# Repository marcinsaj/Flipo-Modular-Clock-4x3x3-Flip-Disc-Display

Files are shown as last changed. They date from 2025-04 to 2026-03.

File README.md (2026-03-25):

# Modular Flip-Disc Clock

>[!TIP]
> If you have issues powering the clock, see the list of [compatible power adapters](https://github.com/marcinsaj/Flipo-Modular-Clock-4x3x3-Flip-Disc-Display/blob/main/datasheet/verified-compatible-power-adapters.md).

## Specification
- the clock consists of two modules: controller module & flip-disc display module
- two buttons for setting the time
- one button for turning on the clock
- accurate real-time clock (RTC) on board RX8025T
- the RTC clock memory is backed up by a supercapacitor, so the clock does not require an additional battery in the event of a power failure or turn off
- clock dimensions: 53 x 137 x 142mm (2.1" x 5.4" x 5.6")
- power supply from USB-C PD 12V
- ISP programming connector - only for intermediate users

## 3D Printed Enclosure
You can print your own enclosure or modify the design:
- [Download STL files on Printables](https://www.printables.com/model/1650064-modular-flip-disc-clock-enclosure)
- [Download the Fusion 360 source file](https://github.com/marcinsaj/Flipo-Modular-Clock-4x3x3-Flip-Disc-Display/raw/main/datasheet/enclosure-modular-flip-disc-clock.f3d)

## Datasheet
  - [CLOCK USER MANUAL](https://github.com/marcinsaj/Flipo-Modular-Clock-4x3x3-Flip-Disc-Display/raw/main/datasheet/Manual-Modular-Flip-Disc-Clock.pdf)
  - [HOW TO READ THE DISPLAY](https://github.com/marcinsaj/Flipo-Modular-Clock-4x3x3-Flip-Disc-Display/raw/main/datasheet/Modular-Flip-Disc-Clock-Symbols.pdf)
  - [FIRMWARE](https://github.com/marcinsaj/Flipo-Modular-Clock-4x3x3-Flip-Disc-Display/blob/main/examples/Firmware-Modular-Flip-Disc-Clock.ino)
  - [4x3x3 flip-disc display module v1 - outdated](https://github.com/marcinsaj/Flipo-Modular-Clock-4x3x3-Flip-Disc-Display/raw/main/datasheet/Modular-Flip-disc-Clock-4x3x3-Display-Module-Schematic-v1.pdf)
  - [4x3x3 flip-disc display module v2 - current version](https://github.com/marcinsaj/Flipo-Modular-Clock-4x3x3-Flip-Disc-Display/raw/main/datasheet/Modular-Flip-disc-Clock-4x3x3-Display-Module-Schematic-v2.pdf)
  - [4x3x3 flip-disc controller module v1 - outdated](https://github.com/marcinsaj/Flipo-Modular-Clock-4x3x3-Flip-Disc-Display/raw/main/datasheet/Modular-Flip-disc-Clock-4x3x3-Controller-Module-Schematic-v1.pdf)
  - [4x3x3 flip-disc controller module v5 - current version](https://github.com/marcinsaj/Flipo-Modular-Clock-4x3x3-Flip-Disc-Display/raw/main/datasheet/Modular-Flip-disc-Clock-4x3x3-Controller-Module-Schematic-v5.pdf)

## Programming and Firmware
If you want to modify the [firmware](https://github.com/marcinsaj/Flipo-Modular-Clock-4x3x3-Flip-Disc-Display/blob/main/examples/Firmware-Modular-Flip-Disc-Clock.ino), you can program the clock via the ISP connector.

### MiniCore Configuration
Before burning the bootloader, install MiniCore using the following Boards Manager URL:
https://mcudude.github.io/MiniCore/package_MCUdude_MiniCore_index.json

### In Arduino IDE → Tools, configure the settings as follows:
- Board: ATmega328P / ATmega328PA
- Clock: External 12 MHz ⚠
- Bootloader: Yes (UART0)
- BOD: 2.7V
- EEPROM: Retained
- Compiler LTO: Enabled
- Baud Rate: Default
- Variant: 328P / 328PA

⚠ Make sure the clock is set to External 12 MHz. ⚠

## Programming Procedure:
 1. Select the correct Programmer: AVR ISP MKII (recommended).
 2. Click Burn Bootloader to set the fuse bits and configure the microcontroller.
 3. After completion, select Upload Using Programmer to flash the firmware.

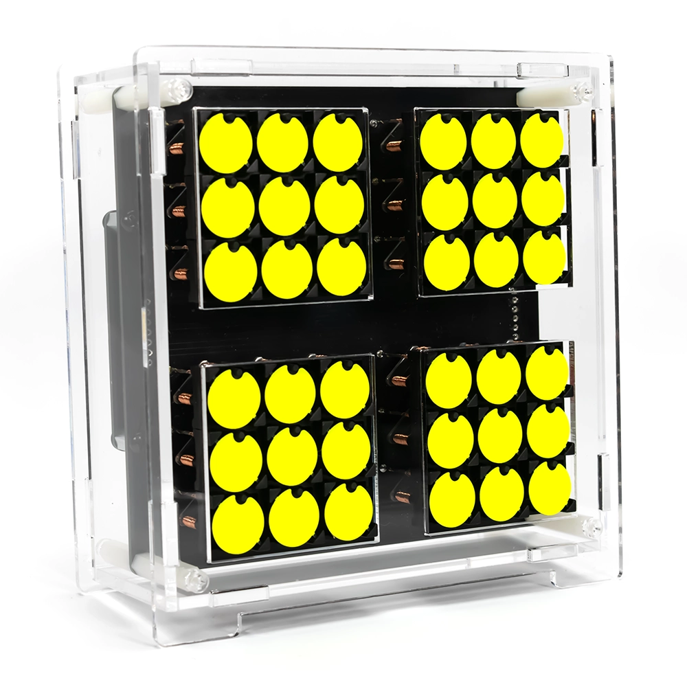
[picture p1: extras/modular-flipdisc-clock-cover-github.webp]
Modular Flip-disc Clock

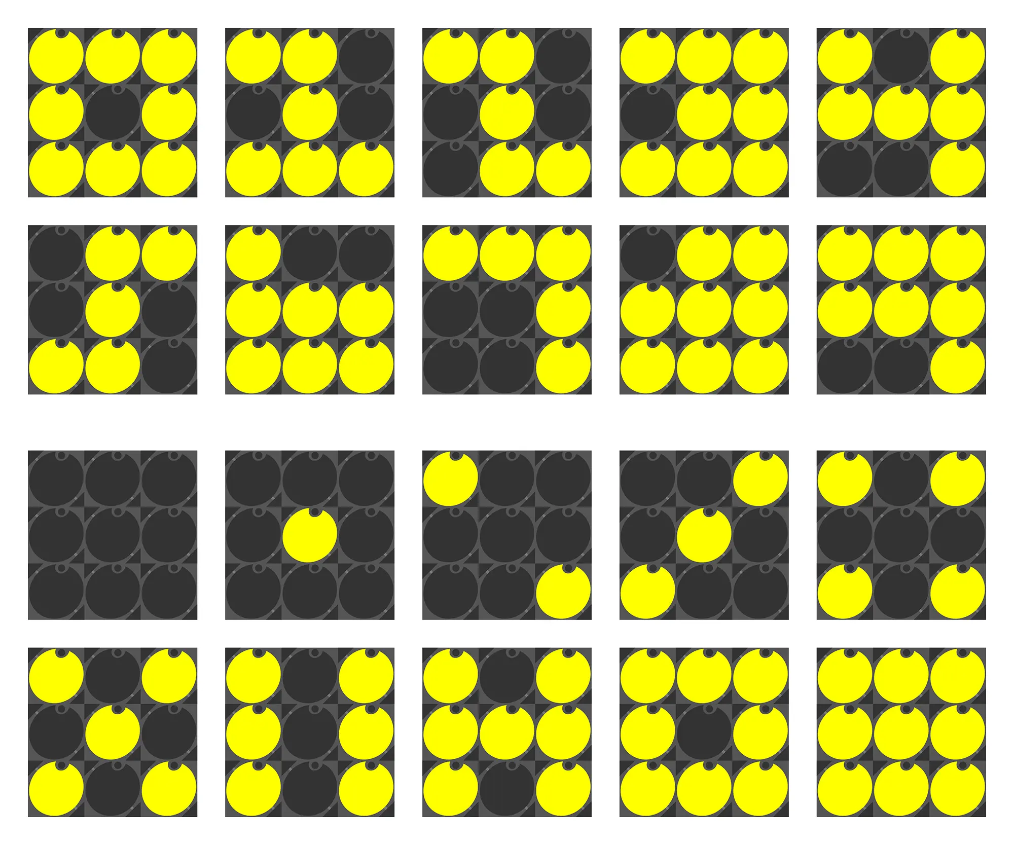
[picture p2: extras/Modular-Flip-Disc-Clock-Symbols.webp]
Modular Flip-disc Clock - Digits

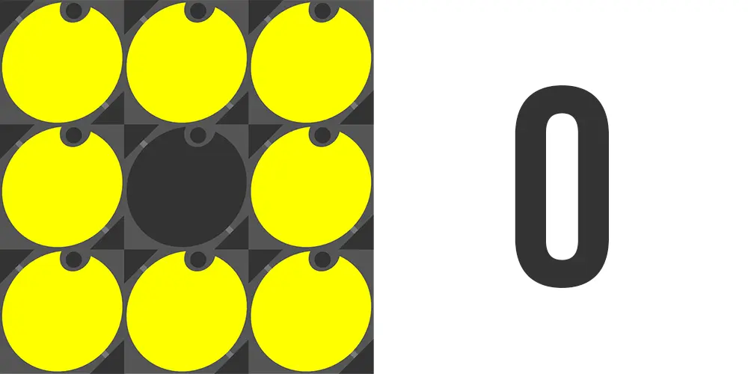
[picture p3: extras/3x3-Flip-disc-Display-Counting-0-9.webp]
Modular Flip-disc Clock - 3x3 Module

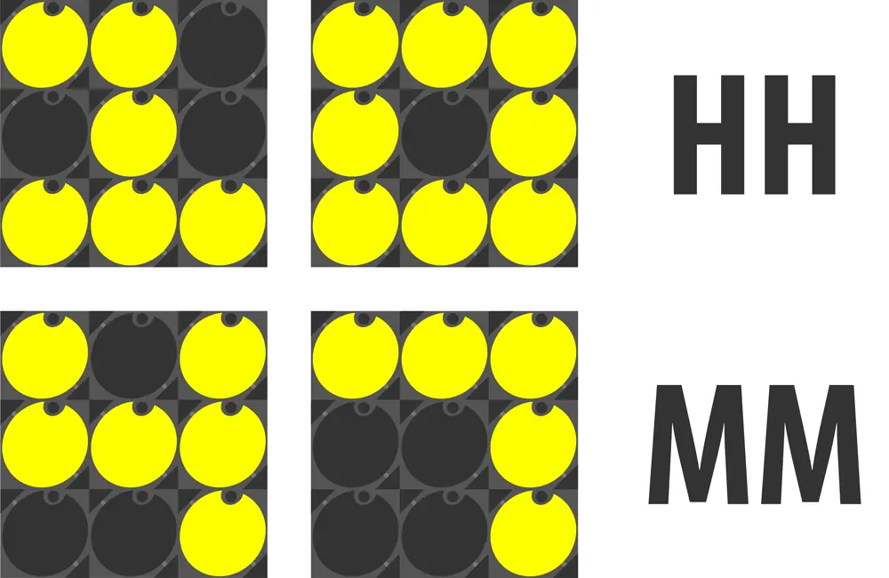
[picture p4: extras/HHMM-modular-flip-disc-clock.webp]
Modular Flip-disc Clock - HH:MM


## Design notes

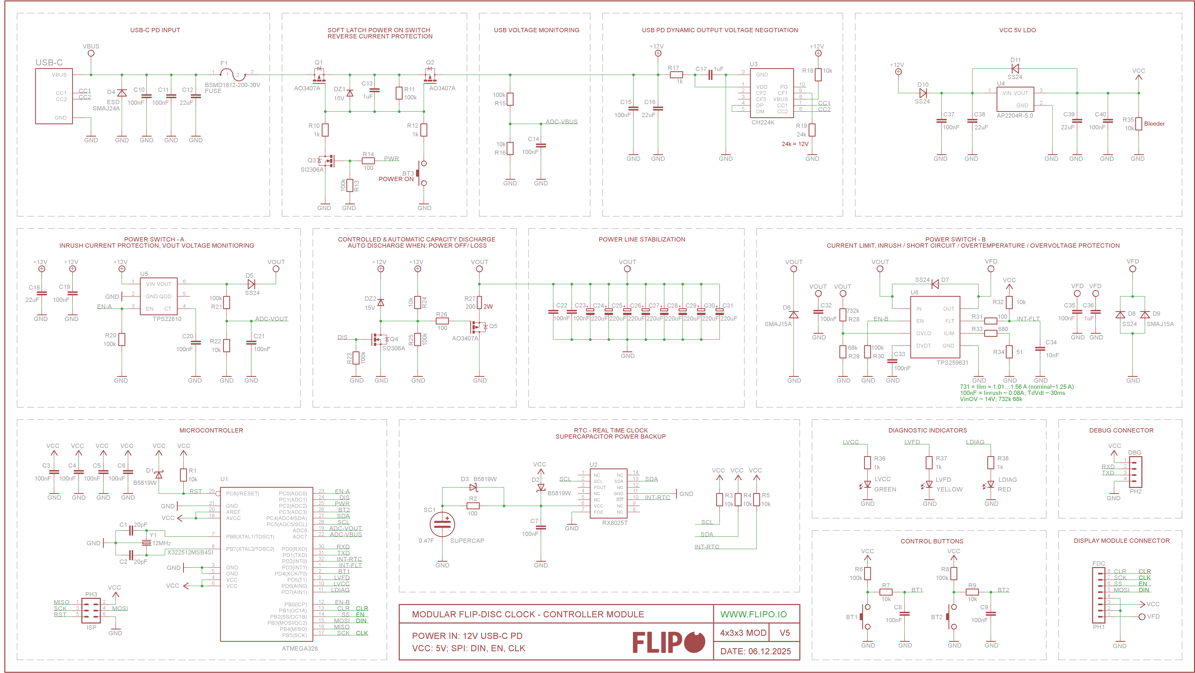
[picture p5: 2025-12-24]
datasheet/Modular-Flip-disc-Clock-4x3x3-Controller-Module-Schematic-v5.png

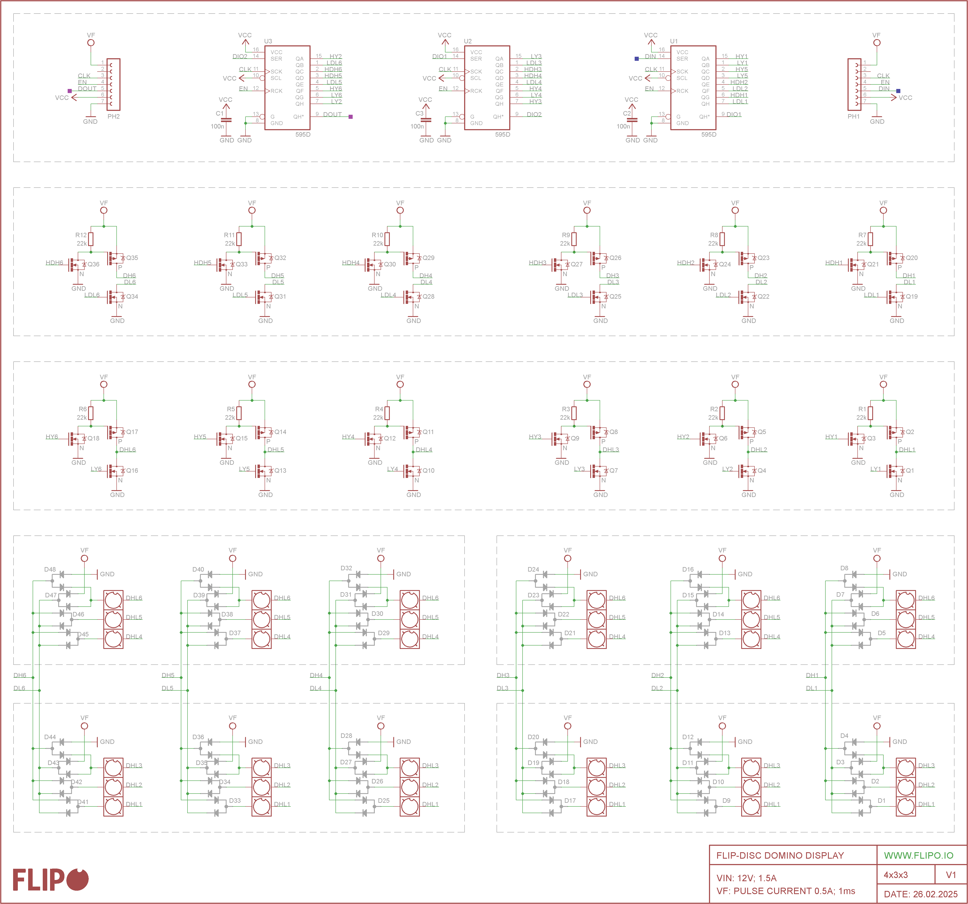
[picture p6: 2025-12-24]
datasheet/Modular-Flip-disc-Clock-4x3x3-Display-Module-Schematic-v1.png

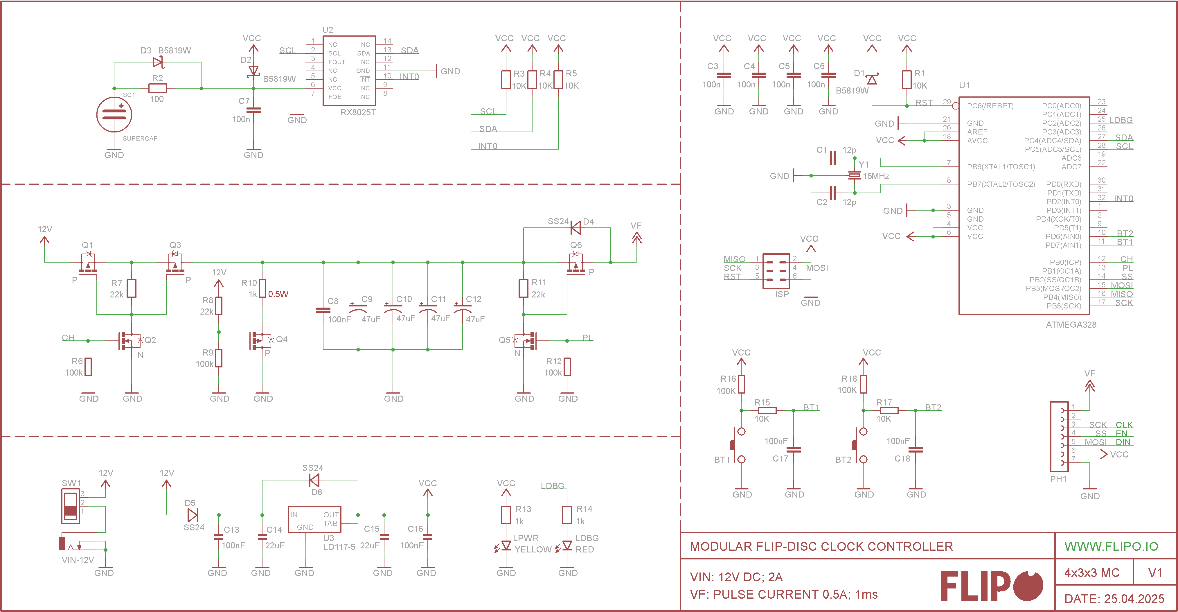
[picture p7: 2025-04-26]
datasheet/Modular-Flip-disc-Clock-4x3x3-Controller-Module-Schematic-v1.png

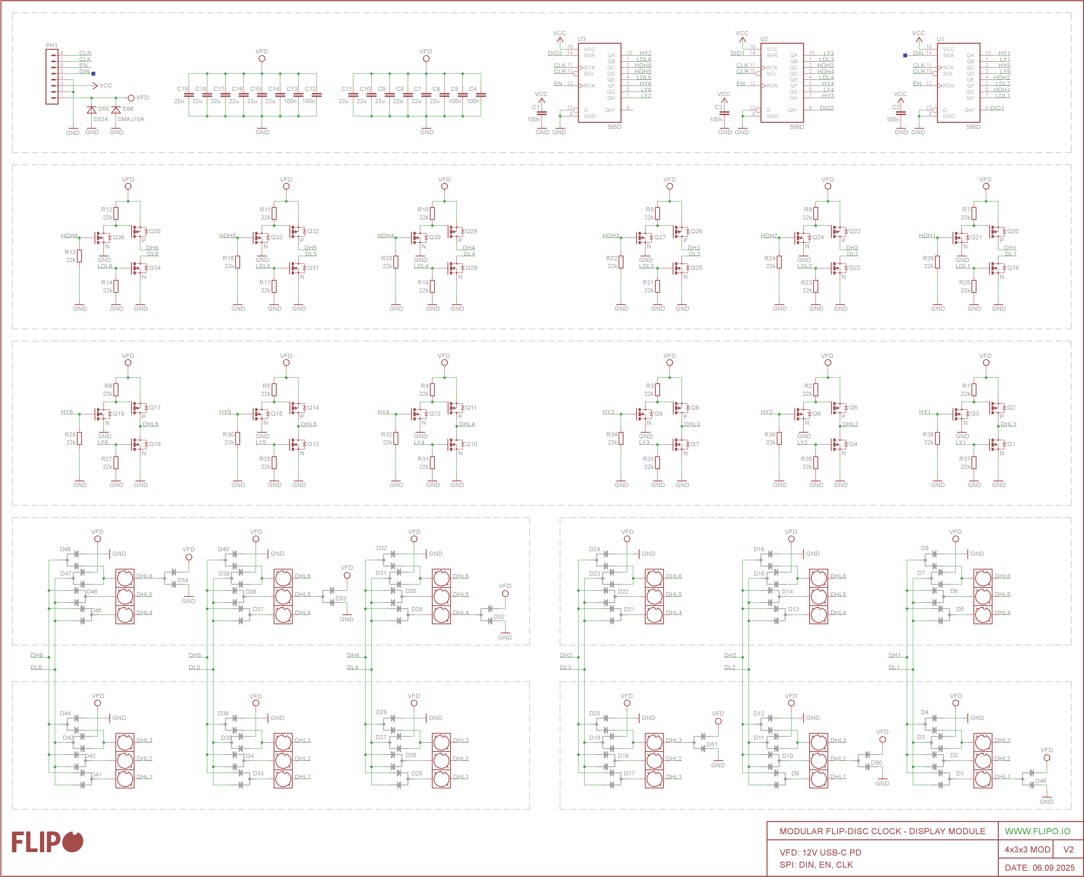
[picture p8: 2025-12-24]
datasheet/Modular-Flip-disc-Clock-4x3x3-Display-Module-Schematic-v2.png

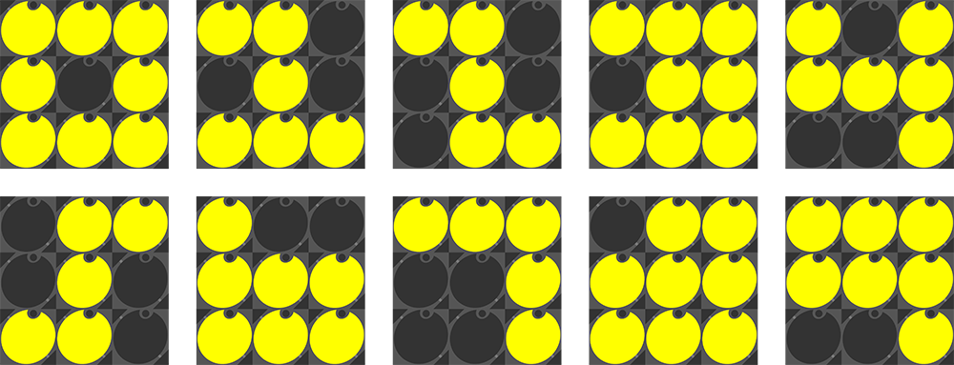
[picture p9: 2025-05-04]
extras/Flipo-3x3-Flip-Disc-Display-Digits-2.png

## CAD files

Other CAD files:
datasheet/enclosure-modular-flip-disc-clock.f3d

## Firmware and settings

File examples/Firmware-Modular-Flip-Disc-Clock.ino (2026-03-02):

/* Modular Flip-disc Clock – Programming and Firmware

MiniCore Configuration
Before burning the bootloader, install MiniCore using the following Boards Manager URL:
https://mcudude.github.io/MiniCore/package_MCUdude_MiniCore_index.json

In Arduino IDE → Tools, configure the settings as follows:
Board: ATmega328P / ATmega328PA
Clock: External 12 MHz
Bootloader: Yes (UART0)
BOD: 2.7V
EEPROM: Retained
Compiler LTO: Enabled
Baud Rate: Default
Variant: 328P / 328PA

⚠ Make sure the clock is set to External 12 MHz. ⚠

Programming Procedure:
1. Select the correct Programmer: AVR ISP MKII (recommended).
2. Click Burn Bootloader to set the fuse bits and configure the microcontroller.
3. After completion, select Upload Using Programmer to flash the firmware. */

#include <RTC_RX8025T.h>  // https://github.com/marcinsaj/RTC_RX8025T
#include <TimeLib.h>      // https://github.com/PaulStoffregen/Time
#include <Wire.h>         // https://arduino.cc/en/Reference/Wire (included with Arduino IDE)
#include <OneButton.h>    // https://github.com/mathertel/OneButton
#include <EEPROM.h>       // (included with Arduino IDE)
#include <SPI.h>          // (included with Arduino IDE)
#include <avr/pgmspace.h> // (included with Arduino IDE)
#include <avr/wdt.h>      // (included with Arduino IDE)


#define DEBUG 0

#if DEBUG
#include <SoftwareSerial.h>

const int RX_PIN = PIN_PD0;
const int TX_PIN = PIN_PD1;

SoftwareSerial mySerial(RX_PIN, TX_PIN);
#endif

// ============================================================================
// FLIP-DISC DISPLAY DATA (PROGMEM)
// ============================================================================
/* Refers to 4x3x3 display.
 * The array contains the addresses of the control outputs corresponding
 * to the setting of the discs to the "color" side.
 * 7,6,5,4,3,2,1,0  15,14,13,12,11,10,9,8  23,22,21,20,19,18,17,16
 *
 *    36 35 34   27 26 25
 *    33 32 31   24 23 22
 *    30 29 28   21 20 19
 *
 *    18 17 16    9  8  7
 *    15 14 13    6  5  4
 *    12 11 10    3  2  1 */
static const uint8_t resetDisc[36][3] PROGMEM =
{
  { 0b00000000, 0b00000000, 0b10000001 },
  { 0b00000000, 0b00000000, 0b00100001 },
  { 0b00000000, 0b00000010, 0b00000001 },

  { 0b00000001, 0b00000000, 0b10000000 },
  { 0b00000001, 0b00000000, 0b00100000 },
  { 0b00000001, 0b00000010, 0b00000000 },

  { 0b00000000, 0b10000000, 0b10000000 },
  { 0b00000000, 0b10000000, 0b00100000 },
  { 0b00000000, 0b10000010, 0b00000000 },


  { 0b00000000, 0b00010000, 0b00000001 },
  { 0b00010000, 0b00000000, 0b00000001 },
  { 0b00000010, 0b00000000, 0b00000001 },

  { 0b00000001, 0b00010000, 0b00000000 },
  { 0b00010001, 0b00000000, 0b00000000 },
  { 0b00000011, 0b00000000, 0b00000000 },

  { 0b00000000, 0b10010000, 0b00000000 },
  { 0b00010000, 0b10000000, 0b00000000 },
  { 0b00000010, 0b10000000, 0b00000000 },


  { 0b00000000, 0b00100000, 0b10000000 },
  { 0b00000000, 0b00100000, 0b00100000 },
  { 0b00000000, 0b00100010, 0b00000000 },

  { 0b00000000, 0b00000000, 0b10000100 },
  { 0b00000000, 0b00000000, 0b00100100 },
  { 0b00000000, 0b00000010, 0b00000100 },

  { 0b00100000, 0b00000000, 0b10000000 },
  { 0b00100000, 0b00000000, 0b00100000 },
  { 0b00100000, 0b00000010, 0b00000000 },


  { 0b00000000, 0b00110000, 0b00000000 },
  { 0b00010000, 0b00100000, 0b00000000 },
  { 0b00000010, 0b00100000, 0b00000000 },

  { 0b00000000, 0b00010000, 0b00000100 },
  { 0b00010000, 0b00000000, 0b00000100 },
  { 0b00000010, 0b00000000, 0b00000100 },

  { 0b00100000, 0b00010000, 0b00000000 },
  { 0b00110000, 0b00000000, 0b00000000 },
  { 0b00100010, 0b00000000, 0b00000000 }
};

static const uint8_t setDisc[36][3] PROGMEM =
{
  { 0b00000000, 0b00000000, 0b01000010 },
  { 0b00000000, 0b00000000, 0b00010010 },
  { 0b00000000, 0b00000100, 0b00000010 },

  { 0b10000000, 0b00000000, 0b01000000 },
  { 0b10000000, 0b00000000, 0b00010000 },
  { 0b10000000, 0b00000100, 0b00000000 },

  { 0b00000000, 0b00000001, 0b01000000 },
  { 0b00000000, 0b00000001, 0b00010000 },
  { 0b00000000, 0b00000101, 0b00000000 },


  { 0b00000000, 0b00001000, 0b00000010 },
  { 0b00001000, 0b00000000, 0b00000010 },
  { 0b00000100, 0b00000000, 0b00000010 },

  { 0b10000000, 0b00001000, 0b00000000 },
  { 0b10001000, 0b00000000, 0b00000000 },
  { 0b10000100, 0b00000000, 0b00000000 },

  { 0b00000000, 0b00001001, 0b00000000 },
  { 0b00001000, 0b00000001, 0b00000000 },
  { 0b00000100, 0b00000001, 0b00000000 },


  { 0b00000000, 0b01000000, 0b01000000 },
  { 0b00000000, 0b01000000, 0b00010000 },
  { 0b00000000, 0b01000100, 0b00000000 },

  { 0b00000000, 0b00000000, 0b01001000 },
  { 0b00000000, 0b00000000, 0b00011000 },
  { 0b00000000, 0b00000100, 0b00001000 },

  { 0b01000000, 0b00000000, 0b01000000 },
  { 0b01000000, 0b00000000, 0b00010000 },
  { 0b01000000, 0b00000100, 0b00000000 },


  { 0b00000000, 0b01001000, 0b00000000 },
  { 0b00001000, 0b01000000, 0b00000000 },
  { 0b00000100, 0b01000000, 0b00000000 },

  { 0b00000000, 0b00001000, 0b00001000 },
  { 0b00001000, 0b00000000, 0b00001000 },
  { 0b00000100, 0b00000000, 0b00001000 },

  { 0b01000000, 0b00001000, 0b00000000 },
  { 0b01001000, 0b00000000, 0b00000000 },
  { 0b01000100, 0b00000000, 0b00000000 }
};

/* Compressed array of all bits corresponding to discs states for selected dice symbol 0-9.
 * 4x3x3 display contains 4 sections 3x3, the discs in each section are numbered in the same way
 * so the array only needs to contain the disc numbers of one section.
 * Disc numbers in individual bytes: 7,6,5,4,3,2,1,0  15,14,13,12,11,10,9,8 */
static const uint8_t diceArray[12][2] PROGMEM =
{
  {0b00000000, 0b00000000}, // 0
  {0b00010000, 0b00000000}, // 1
  {0b00000001, 0b00000001}, // 2
  {0b01010100, 0b00000000}, // 3
  {0b01000101, 0b00000001}, // 4
  {0b01010101, 0b00000001}, // 5
  {0b01101101, 0b00000001}, // 6
  {0b01111101, 0b00000001}, // 7
  {0b11101111, 0b00000001}, // 8
  {0b11111111, 0b00000001}, // 9
  {0b00000000, 0b00000000}, // 10/CAD - clear all discs
  {0b11111111, 0b00000001}  // 11/SAD - set all discs
};

/* Compressed array of all bits corresponding to discs states for selected digits symbol 0-9.
 * 4x3x3 display contains 4 sections 3x3, the discs in each section are numbered in the same way
 * so the array only needs to contain the disc numbers of one section.
 * Disc numbers in individual bytes: 7,6,5,4,3,2,1,0  15,14,13,12,11,10,9,8 */
static const uint8_t numbArray[12][2] PROGMEM =
{
  {0b11101111, 0b00000001}, // 0
  {0b10010111, 0b00000001}, // 1
  {0b10010011, 0b00000001}, // 2
  {0b11011111, 0b00000001}, // 3
  {0b01111001, 0b00000001}, // 4
  {0b11010110, 0b00000000}, // 5
  {0b00111111, 0b00000001}, // 6
  {0b11001001, 0b00000001}, // 7
  {0b11111111, 0b00000000}, // 8
  {0b11111001, 0b00000001}, // 9
  {0b00000000, 0b00000000}, // 10/CAD - clear all discs
  {0b11111111, 0b00000001}  // 11/SAD - set all discs
};

// ============================================================================
// CONSTANTS
// ============================================================================

// Delay between flipping consecutive discs
// Best visual effect in range 0-50ms, maximum value 255
static const uint8_t flip_disc_delay = 30;

// Codenames for the flip-disc display
static const uint8_t CAD = 10; // Clear all discs
static const uint8_t SAD = 11; // Set all discs

// Voltage monitoring thresholds
const int LOWER_THRESHOLD = 200;    // 180 for 10V lower threshold (in ADC units)
const int UPPER_THRESHOLD = 250;   // upper threshold (in ADC units)
const int REQUIRED_OK_SAMPLE = 5;  // number of consecutive in-range readings required
const int SAMPLE_DELAY_MS = 10;    // delay between measurements

// Error / state codes
const int ERROR_NONE = 0;
const int ERROR_VBUS_LOW = 1;   // Vbus <= LOWER_THRESHOLD
const int ERROR_VBUS_HIGH = 2;  // Vbus >= UPPER_THRESHOLD
const int ERROR_VFD_NO_DISPLAY = 3;
const int ERROR_VFD_OVER_CURRENT = 4;

// Aliases for individual option settings
static const uint8_t HR12 = 12;  // Display time in 12 hour format
static const uint8_t HR24 = 24;  // Display time in 24 hour format
static const uint8_t NUMB = 0;   // Display digits in normal mode
static const uint8_t DICE = 1;   // Display digits in dice mode
static const uint8_t E00M = 0;   // Random Effect turn off
static const uint8_t E01M = 1;   // Random Effect every 1 minute
static const uint8_t E60M = 2;   // Random Effect every full hour

// Number of middle sequence cycles (random ON -> random OFF) depending on mode:
// - Every minute (E01M): 1 middle cycle
// - Every hour (E60M): 2 middle cycles
//
// Full effect sequence:
// 1. Randomly turn OFF only currently-ON discs (old time disappears)
// 2. Middle sequence: random ON all -> random OFF all (repeated N times)
// 3. Randomly turn ON only discs needed to display the new time
static const uint8_t EFFECT_MINUTE = 1;
static const uint8_t EFFECT_HOUR = 2;

// Eeprom addresses where settings are stored
static const uint16_t ee_time_format_address = 0;       // Time format 12/24 hour
static const uint16_t ee_symbol_type_address = 1;       // Digits or Dice symbols
static const uint16_t ee_effect_interval_address = 2;   // Random Effect 1min/1hour interval

// ============================================================================
// PIN DECLARATIONS
// ============================================================================

// Analog voltage monitor pins
const int ADC_VBUS_PIN = A7;
const int ADC_VOUT_PIN = A6;

// SPI pins
const int DIN_PIN = PIN_PB3;  // SPI - MOSI
const int EN_PIN  = PIN_PB2;  // SPI - SS
const int CLK_PIN = PIN_PB5;  // SPI - SCK
const int CLR_PIN = PIN_PB1;  // SPI - MISO

// Buttons
const int BT1_PIN = PIN_PD4;  // Right button
const int BT2_PIN = PIN_PC3;  // Left button

// RTC
const int INT_RTC = PIN_PD2;  // RTC interrupt input

// Fault input
const int INT_FLT = PIN_PD3;  // Diagnostic input

// LED - Used to indicate potential hardware issues during the boot process
const int LVCC_PIN = PIN_PD6;   // VCC
const int LVFD_PIN = PIN_PD5;   // VFD
const int LDIAG_PIN = PIN_PD7;  // DIAG

// Power switches
const int ENA_PIN = PIN_PC0;  // High side power switch TPS1H100B
const int ENB_PIN = PIN_PB0;  // Last stand power switch

// Discharge
const int DIS_PIN = PIN_PC1;

// Power ON
const int PWR_PIN = PIN_PC2;

// ============================================================================
// GLOBAL VARIABLES
// ============================================================================

// Time structure and variables
tmElements_t tm;
uint8_t currentTimeDigit[4] = {0, 0, 0, 0};
uint16_t hour_time = 0;
uint16_t minute_time = 0;

// OneButton instances
OneButton button1(BT1_PIN, true, true);
OneButton button2(BT2_PIN, true, true);

// Button press status flags
bool shortPressButton1Status = false;
bool shortPressButton2Status = false;
bool longPressButton1Status = false;
bool longPressButton2Status = false;
bool doubleClickButton1Status = false;

// Settings and status flags
bool powerClockStatus = false;
bool timeSettingsStatus = false;
bool effectSettingsStatus = false;

// Settings values (stored in eeprom, read during setup)
uint8_t time_format = 12;     // HR12 - Time format
uint8_t symbol_type = 0;      // NUMB - Numbers
uint8_t effect_interval = 1;  // Random Effect every 1 minute

// Interrupt flags
volatile bool interruptFltStatus = false;
volatile bool interruptRtcStatus = false;

// Boolean state arrays for all 36 discs (true = ON, false = OFF).
// current_state[] - current display state (old time, before update)
// target_state[]  - target display state (new time, after update)
// Populated by ComputeDisplayState(), used by the visual effect.
bool current_state[36];
bool target_state[36];

// ============================================================================
// INTERRUPT SERVICE ROUTINES
// ============================================================================

void fltInterruptISR(void)
{
  interruptFltStatus = true;
  // Feature planned for future implementation
}

void rtcInterruptISR(void)
{
  interruptRtcStatus = true;
}

// ============================================================================
// BUTTON CALLBACKS
// ============================================================================

void ShortPressButton1(void)
{
  shortPressButton1Status = true;
}

void ShortPressButton2(void)
{
  shortPressButton2Status = true;
}

void LongPressButton1(void)
{
  longPressButton1Status = true;
}

void LongPressButton2(void)
{
  longPressButton2Status = true;
}

void DoubleClickButton1(void)
{
  doubleClickButton1Status = true;
}

void ClearPressButtonFlags(void)
{
  shortPressButton1Status = false;
  shortPressButton2Status = false;
  longPressButton1Status = false;
  longPressButton2Status = false;
  doubleClickButton1Status = false;
}

// ============================================================================
// SETUP
// ============================================================================
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
void loop()
{
  wdt_reset();
  WatchButtons();

  // Handle the per-minute RTC interrupt.
  // Every minute the RTC generates an interrupt that sets the interruptRtcStatus flag.
  //
  // Two visual effect modes:
  // - E01M (every minute): visual effect on every interrupt
  //   (EFFECT_MINUTE middle cycles)
  // - E60M (every hour): effect only on the full hour (minutes == 0)
  //   (EFFECT_HOUR middle cycles), otherwise DisplayRawTime.
  if(interruptRtcStatus == true) DisplayTime();
  if(timeSettingsStatus == true) TimeSettings();
  if(effectSettingsStatus == true) EffectSettings();
}

void GetRtcTime(void)
{
  RTC_RX8025T.read(tm);

  hour_time = tm.Hour;
  minute_time = tm.Minute;

  // 12-Hour conversion
  if(time_format == HR12)
  {
    if(hour_time > 12) hour_time = hour_time - 12;
    if(hour_time == 0) hour_time = 12;
  }

  // Split time into 4 individual digits
  // currentTimeDigit[3] = tens of hours  (e.g. 1 from "14:25")
  // currentTimeDigit[2] = units of hours (e.g. 4 from "14:25")
  // currentTimeDigit[1] = tens of minutes  (e.g. 2 from "14:25")
  // currentTimeDigit[0] = units of minutes (e.g. 5 from "14:25")
  currentTimeDigit[3] = hour_time / 10;
  currentTimeDigit[2] = hour_time % 10;
  currentTimeDigit[1] = minute_time / 10;
  currentTimeDigit[0] = minute_time % 10;
}

// ============================================================================
// DISPLAY RAW TIME
// ============================================================================

void DisplayRawTime(void)
{
  interruptRtcStatus = false;

  for(uint8_t sector = 1; sector <= 4; sector++)
  {
    FlipDisplay(sector, currentTimeDigit[sector - 1], symbol_type);
  }
}

// ============================================================================
// DISPLAY TIME
// ============================================================================

void DisplayTime(void)
{
  interruptRtcStatus = false;

  // Compute current display state BEFORE reading new time
  // (currentTimeDigit[] still contains the OLD time)
  ComputeDisplayState(current_state);

  GetRtcTime();

  // Compute target display state for the NEW time
  // (currentTimeDigit[] has been updated by GetRtcTime)
  ComputeDisplayState(target_state);

  if(effect_interval == E00M)
  {
    DisplayRawTime();
  }
  else if(effect_interval == E01M)
  {
    RandomTimeEffect(minute_time == 0 ? EFFECT_HOUR : EFFECT_MINUTE);
  }
  else if(effect_interval == E60M)
  {
    if(minute_time == 0) RandomTimeEffect(EFFECT_HOUR);
    else DisplayRawTime();
  }
}

// ============================================================================
// RANDOM TIME EFFECT
// ============================================================================

/*
 * ComputeDisplayState() - Computes the state of all 36 discs based on currentTimeDigit[].
 *
 * The state_array parameter is a pointer to a bool[36] array where the result is stored.
 * Called twice in DisplayTime():
 * - BEFORE GetRtcTime() with current_state[] -> OLD time state (what is currently on the display)
 * - AFTER GetRtcTime() with target_state[]    -> NEW time state (what should be displayed)
 *
 * The numbArray/diceArray tables store digit patterns 0-9 as compressed bits:
 * - numbArray[digit][0] = disc bits 0-7 (first byte)
 * - numbArray[digit][1] = disc bit 8 (second byte, only bit 0)
 *
 * Result in state_array[0..35]:
 * - indices 0-8:   section 1
 * - indices 9-17:  section 2
 * - indices 18-26: section 3
 * - indices 27-35: section 4
 */
void ComputeDisplayState(bool* state_array)
{
  for(uint8_t section = 1; section <= 4; section++)
  {
    uint8_t row_index = currentTimeDigit[section - 1];

    for(uint8_t disc_number = 0; disc_number < 9; disc_number++)
    {
      uint8_t bit_number;
      uint8_t column_index;

      if(disc_number < 8)
      {
        bit_number = disc_number;
        column_index = 0;
      }
      else
      {
        bit_number = disc_number - 8;
        column_index = 1;
      }

      bool disc_status;
      if(symbol_type == DICE) disc_status = ((pgm_read_byte(&diceArray[row_index][column_index])) >> (bit_number)) & 0b00000001;
      else                    disc_status = ((pgm_read_byte(&numbArray[row_index][column_index])) >> (bit_number)) & 0b00000001;

      uint8_t idx = disc_number + 9 * (section - 1);
      state_array[idx] = disc_status;
    }
  }
}

/*
 * RandomFlipOffCurrent() - Randomly turns OFF only the discs that are currently ON.
 *
 * First step of the visual effect: the old time "disappears" from the display.
 * Operates only on discs marked as ON in current_state[],
 * making the effect faster (fewer discs to flip)
 * and more precise — only discs forming the old time are turned off.
 *
 * Algorithm: Fisher-Yates shuffle on the subset of ON discs.
 */
void RandomFlipOffCurrent(void)
{
  // Collect disc numbers (1-36) that are currently ON
  uint8_t on_discs[36];
  uint8_t on_count = 0;

  for(uint8_t i = 0; i < 36; i++)
  {
    if(current_state[i])
    {
      on_discs[on_count] = i + 1;  // 1-36 numbering for FlipDisc()
      on_count++;
    }
  }

  // Fisher-Yates shuffle — random permutation of on_discs array
  // Guard: when on_count == 0, expression (on_count - 1) for uint8_t = 255 (underflow)
  if(on_count > 1)
  {
    for(uint8_t i = on_count - 1; i > 0; i--)
    {
      uint8_t j = random(0, i + 1);
      uint8_t temp = on_discs[i];
      on_discs[i] = on_discs[j];
      on_discs[j] = temp;
    }
  }

  // Turn OFF each disc in the shuffled order
  for(uint8_t i = 0; i < on_count; i++)
  {
    FlipDisc(on_discs[i], 0);
  }
}

/*
 * RandomFlipOnTarget() - Randomly turns ON only the discs needed to display the new time.
 *
 * Last step of the visual effect: the new time "appears" on the display.
 * Operates only on discs marked as ON in target_state[],
 * so from a blank (black) screen the new time digits randomly emerge.
 *
 * Algorithm: Fisher-Yates shuffle on the subset of target-ON discs.
 */
void RandomFlipOnTarget(void)
{
  // Collect disc numbers (1-36) that should be ON in the new time
  uint8_t on_discs[36];
  uint8_t on_count = 0;

  for(uint8_t i = 0; i < 36; i++)
  {
    if(target_state[i])
    {
      on_discs[on_count] = i + 1;
      on_count++;
    }
  }

  // Fisher-Yates shuffle
  // Guard: when on_count == 0, expression (on_count - 1) for uint8_t = 255 (underflow)
  if(on_count > 1)
  {
    for(uint8_t i = on_count - 1; i > 0; i--)
    {
      uint8_t j = random(0, i + 1);
      uint8_t temp = on_discs[i];
      on_discs[i] = on_discs[j];
      on_discs[j] = temp;
    }
  }

  // Turn ON each disc in the shuffled order
  for(uint8_t i = 0; i < on_count; i++)
  {
    FlipDisc(on_discs[i], 1);
  }
}

/*
 * RandomTimeEffect() - Main visual effect function for time changes.
 *
 * The middle_cycles parameter sets the number of middle sequence repetitions (ON -> OFF).
 *
 * Full effect sequence:
 *
 * 1. Randomly turn OFF currently-ON discs (old time disappears)
 *    -> operates ONLY on discs forming the old time
 *
 * 2. Middle sequence (repeated middle_cycles times):
 *    -> random ON all 36 discs -> random OFF all 36 discs
 *
 * 3. Randomly turn ON new time discs (new time appears)
 *    -> operates ONLY on discs forming the new time
 *
 * Example every minute (middle_cycles = 1):
 *   [12:34] -> turn off old -> ON->OFF -> turn on new -> [12:35]
 *
 * Example every hour (middle_cycles = 2):
 *   [12:59] -> turn off old -> ON->OFF -> ON->OFF -> turn on new -> [13:00]
 *
 * current_state[] and target_state[] must be computed BEFORE calling
 * this function (in DisplayTime()).
 */
void RandomTimeEffect(uint8_t middle_cycles)
{
  // Step 1: Randomly turn OFF only currently-ON discs
  // Old time disappears from the display disc by disc in random order
  RandomFlipOffCurrent();

  // Step 2: Middle sequence — full flicker (ON -> OFF) repeated N times
  for(uint8_t cycle = 0; cycle < middle_cycles; cycle++)
  {
    RandomFlipDisc(1);
    RandomFlipDisc(0);
  }

  // Step 3: Randomly turn ON only discs needed for the new time
  // New time digits emerge from a blank screen disc by disc
  RandomFlipOnTarget();
}

// ============================================================================
// EFFECT SETTINGS
// ============================================================================
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

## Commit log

2026-02-27 Update README with firmware programming instructions
    Added instructions for programming the firmware via ISP connector and included MiniCore installation instructions.
2026-03-02 Fix capitalization in comment header
    [Firmware-Modular-Flip-Disc-Clock.ino]
2026-03-12 Update header for compatible power supply section
2026-03-12 Update header for compatible power supply section
    Removed the 'IMPORTANT' label from the section header.
2026-03-12 Update US section with important notes
    Added important notes for US power supply compatibility.
2026-03-12 Fix formatting in power supply note section
2026-03-12 Update compatible power supply list
    Added Baseus GaN3 Pro 100W to compatible power supply list.
2026-03-12 Update link for compatible power adapters
2026-03-12 Update power supply section with verified adapters
2026-03-12 Update power supply requirements and compatible adapters
    Added a note about power supply requirements and a list of verified compatible power adapters.
2026-03-12 Fix link to verified compatible power adapters
    Updated link to the list of compatible power adapters.
2026-03-12 Fix formatting of power supply note in datasheet
